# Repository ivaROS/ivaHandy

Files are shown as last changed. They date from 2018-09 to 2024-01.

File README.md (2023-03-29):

# ivaHandy

document and code for Handy arm include tutorials, mechanical files and ROS-related packages.

## Doc

Doc includes tutorials about how to build your own robot arm. Contents contain the whole process starting from
how to do assembly in Solidworks in order to make urdf generation easier to use MoveIt! setup assistant to build
your own robot arm MoveIt! package.

## mechanical

Mechanical includes 3DParts and Assembly two folders. 3DParts folder maintains all the files including Solidworks file,
3Dprinting file and drawing that belong to individual piece. Assembly holds models for the whole arm and each link.

## ros

ros folder keeps all ROS-related packages to the handy arm, which includes description, control, gazebo and MoveIt! package.
There are two versions of Handy, one is the normal model which the other one is mesh-simplified model. Each has the four above packages.

### dependencies

1. If you'd like to use finalarm_gazebo package, you should git clone balabala packages to your workspace since gazebo has dependencies on these packages if you want to load controllers in gazebo.

2. If you just need finalarm_control, finalarm_description and finalarm_moveit_config packages, in order to compile all packages out, you additionally need a package named dynamixel_motor which applies designed controllers for dynamixel motors.

### real world motion planning with Handy

Ensure that the current user is part of the `dialout` group.
If you get permission issues connecting to `/dev/ttyUSB0`, run the following and logout+login.

```bash
sudo usermod -aG dialout $USER
```

Launch handy with the following commands:

```bash
# start a node responsible for managing loaded controllers
roslaunch finalarm_control controller_manager.launch

# load configuration for individual controller
roslaunch finalarm_control start_controller.launch

# publish integrated information of controllers and transformations between links
roslaunch finalarm_description robot_state_pub.launch

# node for motion planning, collision checking, etc. jobs
roslaunch finalarm_moveit_config move_group.launch

# rviz for visualization
roslaunch finalarm_moveit_config moveit_rviz.launch

# launch the file you write for Handy to do something like picking object
roslaunch handy_experiment pick.launch
```

You can run the above using `docker-compose` instead:

```bash
docker-compose up

# node for motion planning, collision checking, etc. jobs
roslaunch finalarm_moveit_config move_group.launch

# rviz for visualization
roslaunch finalarm_moveit_config moveit_rviz.launch
```

Read [docs/docker.md](docs/docker.md) for more details.

## launchfiles

Here's a list of launch files that can be tested without access to the physical robot.

```bash
# check for urdf loading
roslaunch finalarm_description display.launch
# check robot position topics
roslaunch finalarm_description gazebo.launch
roslaunch finalarm_gazebo robot_world.launch
roslaunch finalarm_gazebo robot_world.launch control_mode:=position
# check operation of robot
roslaunch finalarm_moveit_config demo.launch
# check gazebo and moveit operate together
roslaunch finalarm_gazebo robot_world_moveit.launch

roslaunch finalarm_simplified_description display.launch
roslaunch finalarm_simplified_description gazebo.launch
roslaunch finalarm_simplified_gazebo robot_world.launch
roslaunch finalarm_simplified_gazebo robot_world_urdf.launch
roslaunch finalarm_simplified_gazebo robot_world_xacro.launch
roslaunch finalarm_simplified_moveit_config demo.launch
roslaunch finalarm_simplified_gazebo robot_world_moveit.launch
```

These are useful for manual testing, at least until some form of automated testing is implemented.

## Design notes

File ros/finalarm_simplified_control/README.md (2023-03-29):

# finalarm_simplified_control

This package redirects to most of the launch scripts in the `finalarm_control` package.
It is used to launch the controllers for the Handy arm.

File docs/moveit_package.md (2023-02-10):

# generating moveit package

Generation of moveit configuration package can be divided into two parts.
One is use moveit setup assistant to configurate your arm and the other is to modify some files within the automatically generated package.

I will just mention the key points, the rest steps you can follow the official tutorial from MoveIt!.
First you need to create group for your robot arm. Here we have two groups.
The first one is arm group and the other one is end effector group.
For the arm group, you just need setup chain for it.
Chain should starts from the root to the end effector.
For the end effector group, add links of your end effector link and two links belonged to your gripper and joints belonged to your gripper.
Secondly when configurate end effector, choose parent link to be your the end effector link and group to be your end effector group.

1. Add controllers.yaml in config folder
1. Modify finalarm_description_moveit_controller_manager.launch.xml file
1. Change the default argument of config in moveit_rviz.launch to true
1. Optional: you can turn animation loop off in `trajectory_execution.launch.xml`: `<param name="trajectory_execution/execution_duration_monitoring" value="false" />`

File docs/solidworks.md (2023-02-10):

# solidworks

## solidworks assembly

When assembling the arm in Solidworks, try to assemble the parts into different links.
For example, if your arm has 7 DOF which means it has 8 links, you need first get 8 sub-assemblies and then assemble them into the final arm assembly.

The mate between the nearby two links should be one concentric and one coincident.

## assembly to urdf

ROS has developed Solidworks add-in tool for automatical conversion from Solidworks assembly to urdf package.
Here is the link: http://wiki.ros.org/sw_urdf_exporter

There are still a lot of bugs during the process of conversion, here are some tips:

At the beginning, don't manually choose any axis, coordinate or joint type during configuration, just fill in the name of link and joint and choose the part belonged to this link. After build the whole tree of link, press export and it will automatically generate the coordinate and axis.
The joint axis should be correct if the mate is set correctly.

After automatical generation, usually the world coordinate is totally wrong, you can manually set up all coordinates.
If you don't know how to choose the coordinate, you may refer some commercial robot arms like pr2.
In order to have a end effector link, you can set up a coordinate for it and add your eef link to be child of the wrist link.
Remember the joint type between eef link and wrist link should be fixed.
The eef link just helps you conveniently do eef pose computation.
You don't need to always compensate the length of the gripper.

After coordinate is done, go back to the UI of configuration, fill in the coordinate, axis and joint type and export the configuration.
In the post-configuration menu, you can fill in the low and high limit of your joint if you choose your joint type to be revolute.
Remember the automatically generated inertial moments of link are wrong.
You should use Solidworks to get the correct inertial moments of each link relative to your coordinate.
Some mass center and mass can also be wrong.
But make sure that you can't change these parameters in the post-configuration menu.
You'd better change them directly in the urdf file.
Otherwise I assume it will affect the generation of mesh file which finally leads to the unstable of arm model in gazebo.
If you don't need to load the model in gazebo, inertial moments are irelevant to you.

When you create moveit package for your arm model and let it go somewhere, you may find some joints rotate the opposite way.
You just need to flip the joint axis in urdf file and it is fine.

## using the urdf in gazebo

The problem you may meet when load arm model in gazebo is arm is unstable and keeps shaking.
Even worst, it may explode link by link.
In order to make your arm stable in gazebo and implement control for it, here are some tips:

Firstly, turn collision and gravity off to make sure the passive behavior of your arm is correct.
Basically, the inertial moments should be the one needed modification if you generate your urdf from Solidworks.
Then add `<dynamics damping="0.5"/>` tag to each joint tag.
And the effort and velocity tag in joint limit are all zero when generated, you need to set it to a certain value.
If the arm is still unstable after the inertial moments are corrected, you can try to add tag `<implicitSpringDamper>True</implicitSpringDamper>` to each joint.
It may help.
Here is the official tutorial from gazebo, http://gazebosim.org/tutorials/?tut=ros_urdf.

2After the passive behavior of arm is correct, you are close to success and just need to implement ros control.
Here is the official tutorial from gazebo, http://gazebosim.org/tutorials/?tut=ros_control.
My suggesstion is to go through tutorial and find some examples to follow.
There may be some small problems caused by ros version.
When you meet it, just google it and you will find solution.

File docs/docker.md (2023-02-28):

# running Handy on docker and docker-compose

Handy needs python2 to run because of the serial library that is used to talk with the dynamixel motors.
This forces kinetic (possibly melodic) as the primary ROS target, which makes it difficult to use modern tooling (think opencv or pytorch) in concert with the arm.
One solution that is currently employed by the lab is to network the handy code on a machine running Ubuntu 16/18, and to run modern code on another machine.
We can also use docker to encapsulate the ROS modules in the repo, so that the host machine can be on a more modern base system.

## quickstart

Ensure the current user is part of the `dialout` (for access to `/dev/ttyUSB0`) and `docker` groups.

```bash
sudo usermod -aG dialout $USER
sudo usermod -aG docker $USER
```

Logout and login for changes to take effect.
If you are runnning an older version of Ubuntu, you may have `docker` installed, but not `docker-compose`.
Install it via pip.

```bash
pip3 install docker-compose
```

Ensure that the site-packages bin directory is on your path.

At the root of the repository, run the following commands:

```bash
# build the images for the services
docker-compose build

# run the containers
docker-compose up
```

Now you are ready to run rviz.

```bash
roslaunch finalarm_moveit_config move_group.launch
roslaunch finalarm_moveit_config moveit_rviz.launch
```

Note that the move group and the rviz commands have to be done with the same version with moveit.
If we try to run rviz commands from a noetic host on the kinetic container, we will run into protocol issues.

## Dockerfile

The `Dockerfile` contains all the dependencies for the project.
The main steps are as follows:

- Installing build dependencies (gcc, git, etc)
- Configuring `rosdep`
- Adding dynamixel dependenices
- Initializing the catkin workspace
- Adding the handy repo to the catkin workspace
- Building all dependencies

We derive our Dockerfile from `ros:kinetic-ros-core-xenial`, which lets us set an environment that can be run on any machine.
We also need to configure a catkin workspace on the container, so we can install our external dependencies and the current repo.
We end up with the following directory structure under the `/app` folder.

```
/app
├── bin
├── build
├── devel
│   ├── include
│   ├── lib
│   └── share
└── src
    ├── ivaDynamixel
    └── ivaHandy
```

We create a `bin` directory that contains useful scripts in the context of our containerized process.
The first is `ros_entrypoint.sh`, which is a simple wrapper that activates `devel/setup.bash` and runs an arbitrary command e.g. `rostopic list`.
The second script is `wait_for_topic_pattern.sh`, which we use to ensure that dependencies are created appropriately when we bring up a series of containers.

## docker-compose

The `docker-compose.yml` contains the containers necessary for running Handy.
Refer to the README for the purpose of each stage.

```mermaid
graph TD
    master
    master --> controller
    controller -.-> start_controller
    start_controller -.->|inits motors| robot_state_pub
    controller --> robot_state_pub
    robot_state_pub --> move_group

    master --> robot_state_pub
    master --> move_group
```

We create a separate master node that runs `roscore` and handles IPC between the various nodes.
Each of the processes is put into their own network i.e. the controller manager, robot state publisher, and the moveit group.
Generally in docker compose, we set up an isolated network where containers communicate with each other via internal DNS.
However, resolving hostnames of each of the containers requires us to set various parameters e.g. `ROS_HOSTNAME` and `ROS_MASTER_URI`.
Instead, we simplify the configuration by assuming that we are using the host network.
This means that all of the containers can reach each other using `localhost`, but we also lose a degree of host (and cluster) isolation.

There are a few other sections to note, if you have never used docker compose before. When using a device, we need to explicitly declare it.

```yaml
    devices:
      - /dev/ttyUSB0
    privileged: true
```

Setting `devices` here is basically the equivalent as marking it as a volume using `priviledged` mode, but is the better way to expose access to the serial device.
We also set `priviledged` to true, otherwise we run into protocol errors (presumably because of permissions, but the logging information is sparse).

We also mount our local directory into the container:

```yaml
    volumes:
      - ./:/app/src/ivaHandy/
      - ./bin:/app/bin/
```

We can change our code, and simply restart our process.
This can save us from the long build process that's caused by dependency resolution.

There is also a dependency between the different ROS nodes.
We get around this by creating a script that will look for topic creation before moving on to the next stage.
We wrap this inside of a `bash -c` call, because our entrypoint will exec a single command.
If we try to use shell commands like `&&` or `||`, we'll run into strange issues.

```yaml
    command: |
      bash -c "
        bin/wait_for_topic_pattern.sh 'finalarm_position_controller_' &&
        stdbuf -o L roslaunch --wait finalarm_description robot_state_pub.launch
      "
```

The docker-compose configuration should be treated as a reference -- the same patterns can be used on other projects too.
There are some modifications that might need to be made, such as removing the master node (if we assume that a master node exists elsewhere) or passing in an explicit `ROS_MASTER_URI`.

Additionally, here are some handy commands to keep in mind:

```bash
# shell into a new instance of a service
docker-compose run --rm ${service} bash
# e.g.
docker-compose run --rm controller_manager bash

# show the logs for a specific container
docker-compose logs -f ${service}
# e.g.
docker-compose logs -f controller_manager
```

## resources

Here are some useful links:

- https://docs.docker.com/engine/install/linux-postinstall/
- https://docs.docker.com/compose/
- http://wiki.ros.org/docker/Tutorials/Compose
- https://hub.docker.com/_/ros

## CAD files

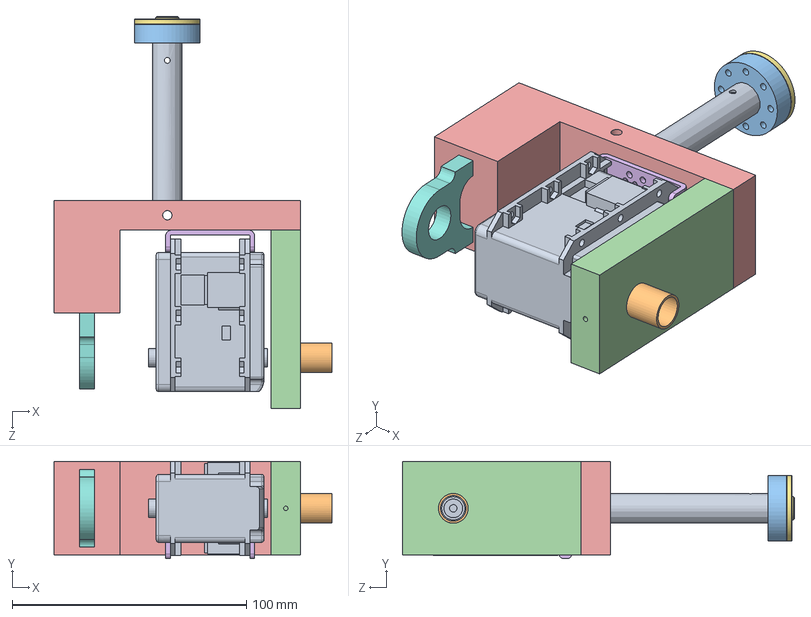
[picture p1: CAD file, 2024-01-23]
mechanical/Assembly/Link2.SLDASM
118.7 x 41.6 x 167.4 mm
at-06_Motor1
at-06-Motor2-2_v2
HN05-N101_to_at-06_attachment_6_27
Motor2Back
Motor2Bottom
FR05-S101
HN05-N101
PillowBlock
EX-106+

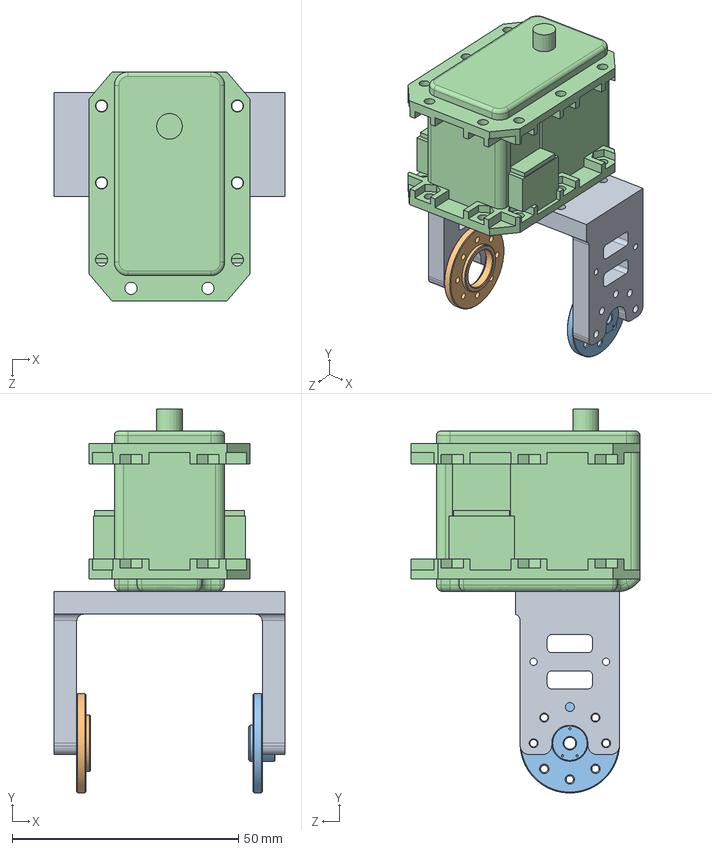
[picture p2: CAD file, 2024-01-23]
mechanical/Assembly/Link7.SLDASM
51.0 x 84.8 x 50.6 mm
myFR07-H101
HN07-i101
HN07-N101
MX-28T_R

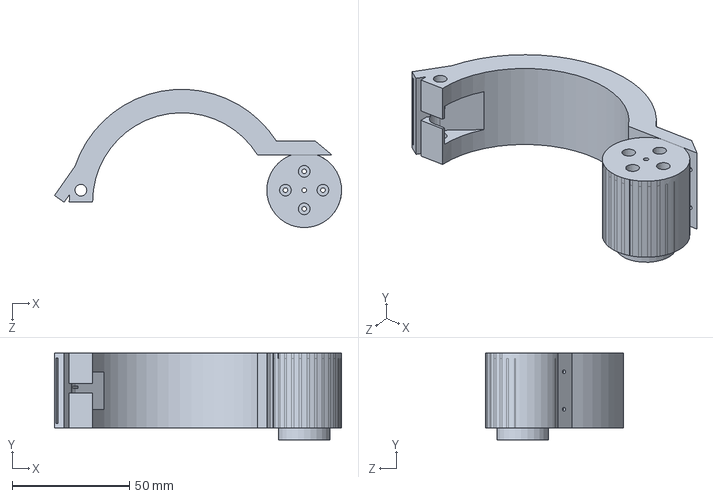
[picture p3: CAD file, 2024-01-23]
mechanical/Assembly/Link9.SLDASM
122.4 x 37.0 x 58.9 mm

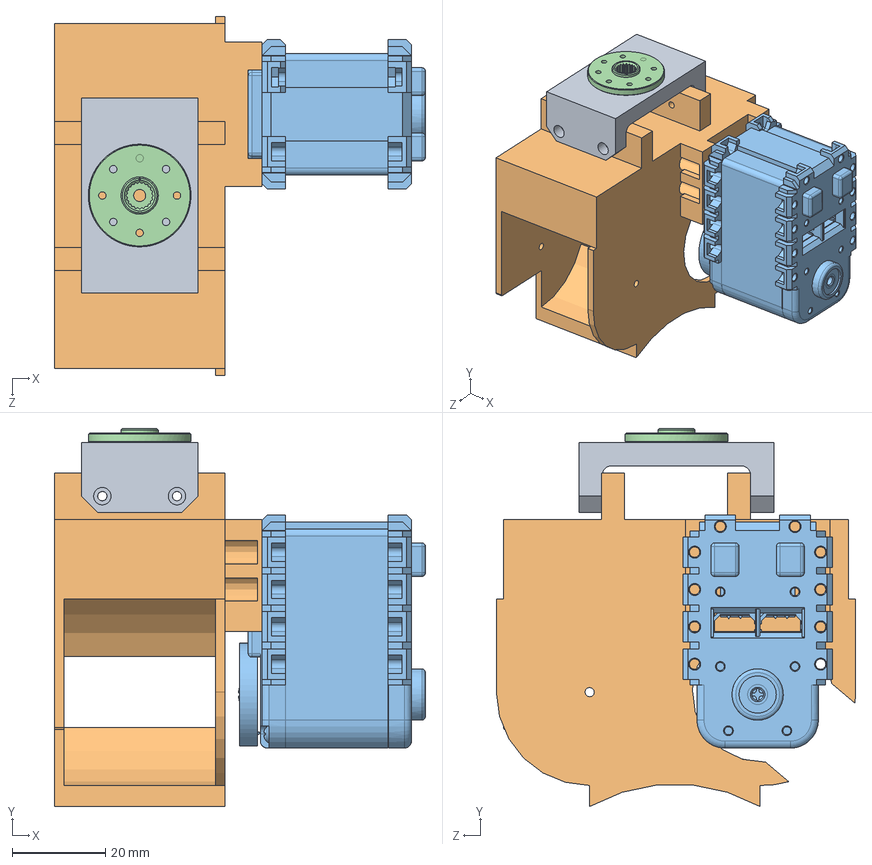
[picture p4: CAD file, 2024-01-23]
mechanical/Assembly/Link8.SLDASM
79.5 x 81.0 x 77.0 mm
GripperAttachment
supporter_cut_36_5
AX-12A
HN07-N101

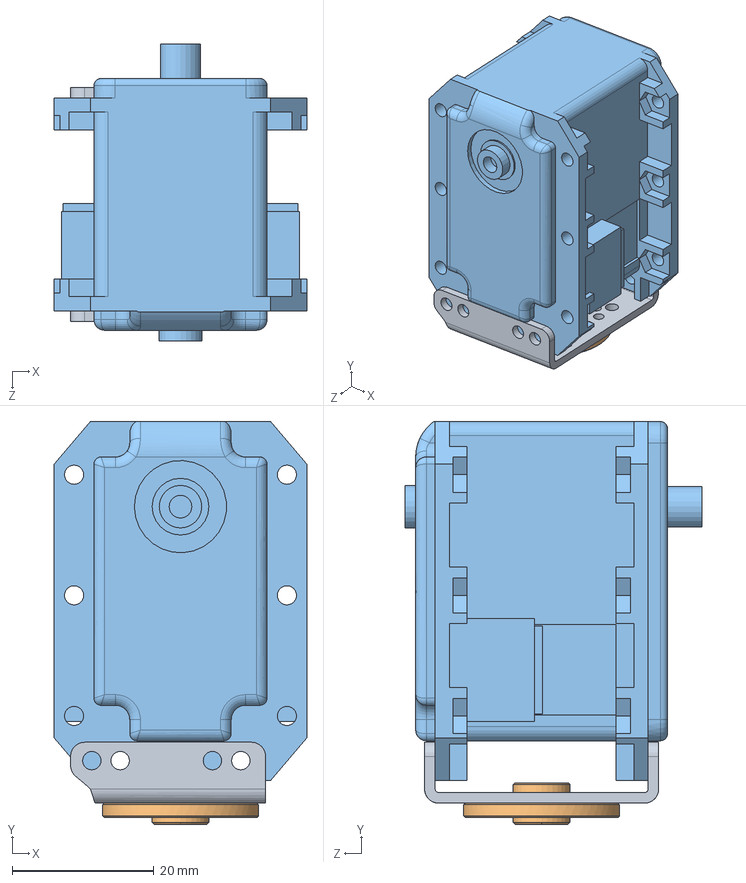
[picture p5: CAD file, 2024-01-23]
mechanical/Assembly/Link6.SLDASM
35.6 x 56.8 x 41.9 mm
FR07-S101
HN07-N101
MX-28T_R

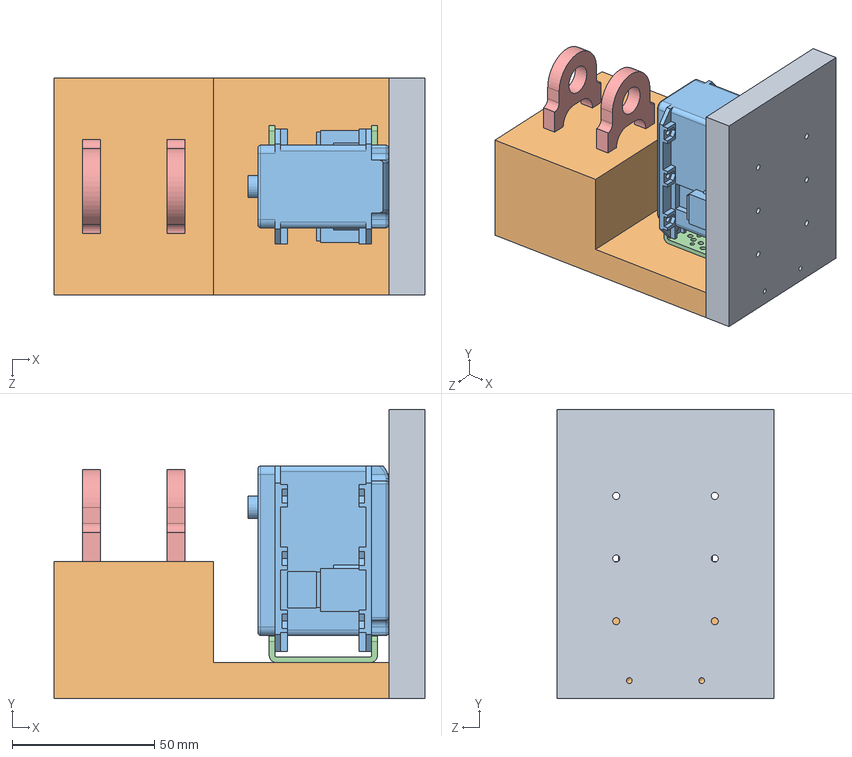
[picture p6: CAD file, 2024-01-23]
mechanical/Assembly/Link1.SLDASM
130.2 x 101.6 x 76.2 mm
Motor1Back
Motor1Bottom
EX-106+
FR05-S101
PillowBlock x 2

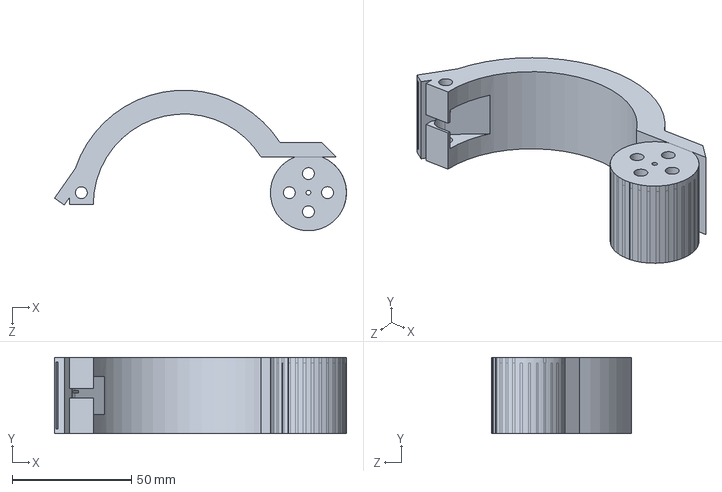
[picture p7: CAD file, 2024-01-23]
mechanical/Assembly/Link10.SLDASM
122.5 x 32.0 x 58.9 mm

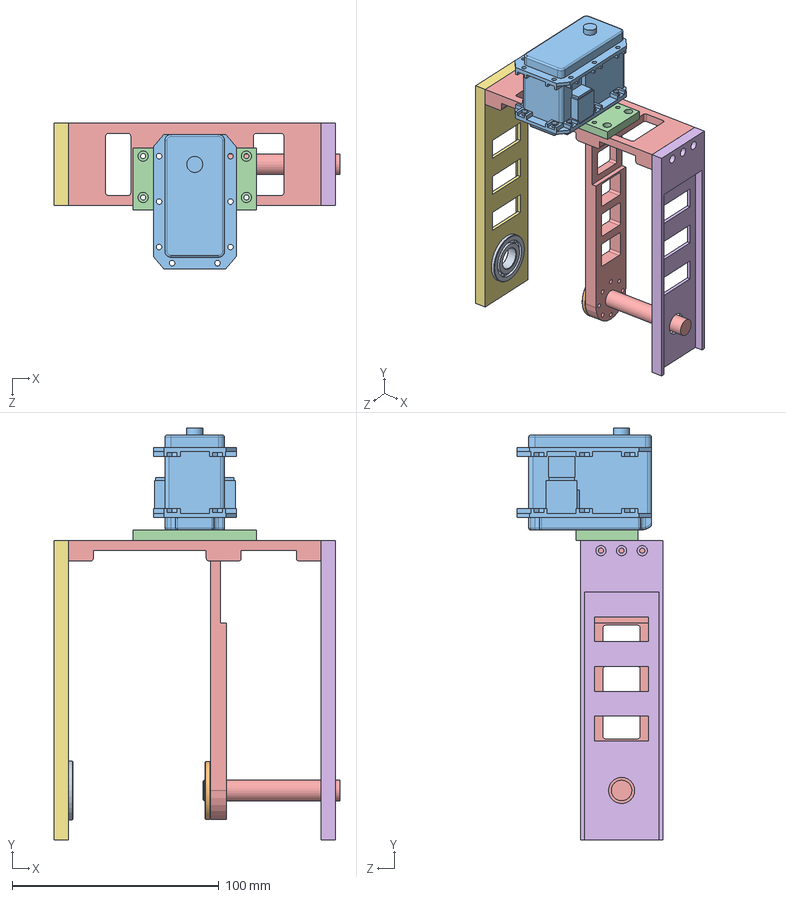
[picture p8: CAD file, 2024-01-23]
mechanical/Assembly/Link3.SLDASM
138.4 x 199.5 x 70.6 mm
BallBearing25
HN05-N101
EX-106+
adapter_ex106
Motor2Frame_HN05-N101_bug_fixed
Motor2Frame_Side1
Motor2Frame_Side2

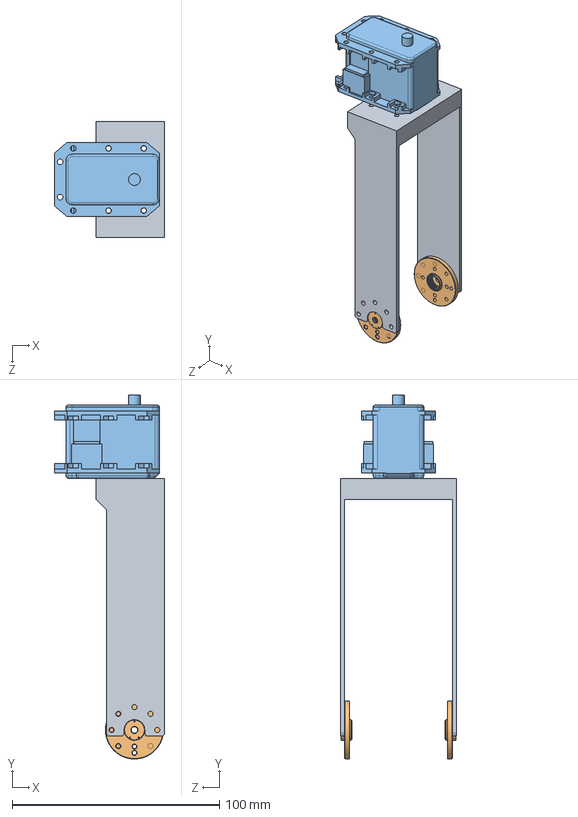
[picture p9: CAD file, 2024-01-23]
mechanical/Assembly/Link5.SLDASM
53.2 x 175.4 x 56.0 mm
myFR08-H101
HN05-N101 x 2
MX-28T_R

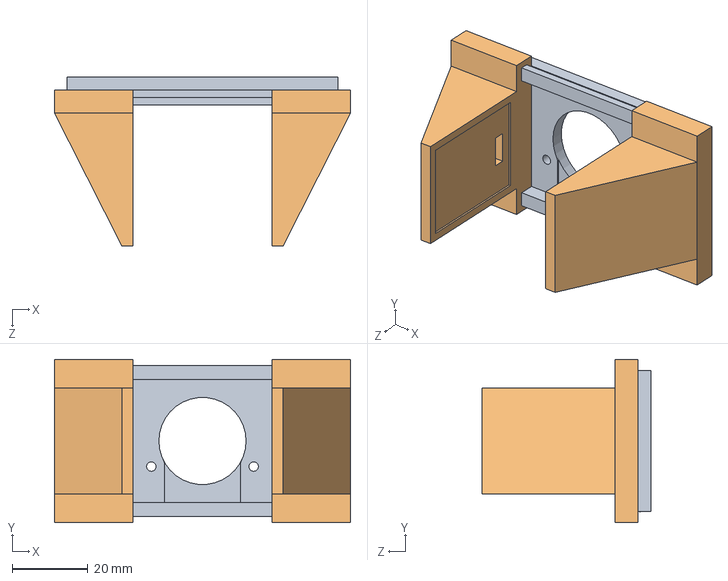
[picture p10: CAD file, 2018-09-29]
mechanical/3DParts/PrefabParts/PX-Gripper.SLDASM
78.1 x 43.0 x 44.5 mm
Guide_Rail_Fixed
Gripper_Hand_Fixed x 2

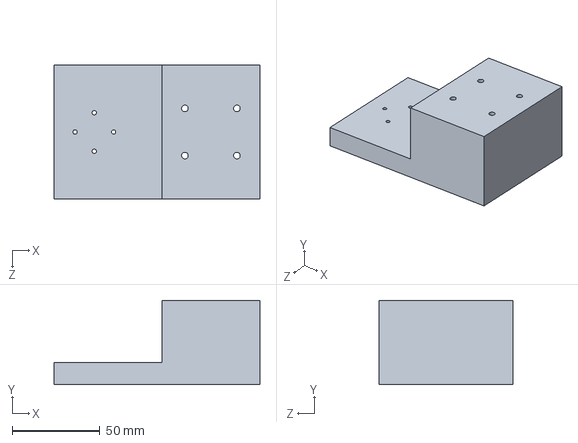
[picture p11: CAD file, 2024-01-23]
mechanical/3DParts/CustomConnectors/Link1/Motor1Bottom.SLDPRT
117.6 x 48.1 x 76.2 mm

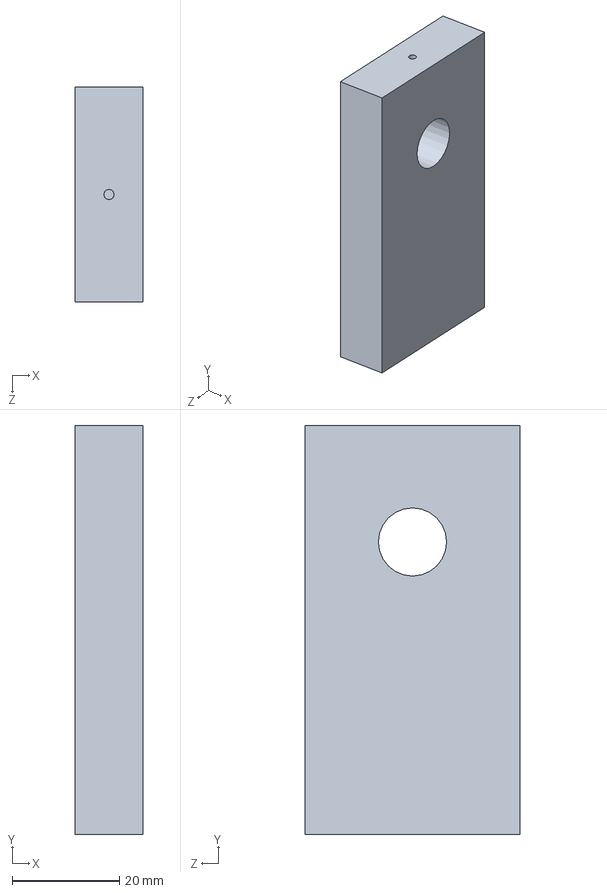
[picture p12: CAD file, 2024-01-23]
mechanical/3DParts/CustomConnectors/Link2/Motor2Back.SLDPRT
12.7 x 76.2 x 40.0 mm

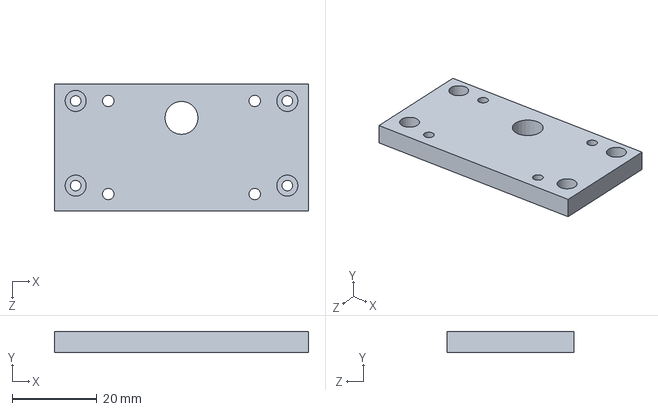
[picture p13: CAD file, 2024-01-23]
mechanical/3DParts/CustomConnectors/Link3/adapter_ex106.SLDPRT
60.0 x 5.00 x 30.0 mm

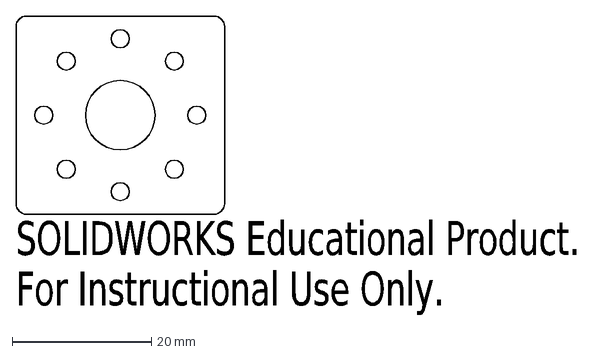
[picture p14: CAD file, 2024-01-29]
mechanical/3DParts/CustomConnectors/Link4/fabrication/HN07-N101-short-ex-ex_horn_reinforcement.DXF
SOLIDWORKS Educational Product.
For Instructional Use Only.

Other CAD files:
mechanical/Assembly/Link4.SLDASM
mechanical/Assembly/finalarm.SLDASM
mechanical/3DParts/CustomConnectors/Link10/r_Finger.SLDPRT
mechanical/3DParts/CustomConnectors/Link4/HN07-N101-short-ex-ex_side_reinforcement.SLDPRT
mechanical/3DParts/CustomConnectors/Link1/Motor1Back.SLDPRT
mechanical/3DParts/CustomConnectors/Link2/HN05-N101_to_at-06_attachment_6_27.SLDPRT
mechanical/3DParts/CustomConnectors/Link2/Motor2Bottom.SLDPRT
mechanical/3DParts/CustomConnectors/Link2/at-06-Motor2-2_v2.SLDPRT
mechanical/3DParts/CustomConnectors/Link2/at-06_Motor1.SLDPRT
mechanical/3DParts/CustomConnectors/Link3/Motor2Frame_HN05-N101_bug_fixed.SLDPRT
mechanical/3DParts/CustomConnectors/Link3/Motor2Frame_Side1.SLDPRT
mechanical/3DParts/CustomConnectors/Link3/Motor2Frame_Side2.SLDPRT
mechanical/3DParts/CustomConnectors/Link3/adapter_mx28.SLDPRT
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

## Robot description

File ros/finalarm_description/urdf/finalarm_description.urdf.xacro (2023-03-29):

<?xml version="1.0" ?>
<robot xmlns:xacro="http://www.ros.org/wiki/xacro" name="finalarm_description">
  <xacro:arg name="use_gazebo" default="false" />

  <xacro:if value="$(arg use_gazebo)">
    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

    <link name="root">
      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
    </link>

    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
    <link name="world" />
    <joint name="connect_root_and_world" type="fixed">
      <parent link="world" />
      <child link="root" />
      <axis xyz="0 0 0" />
      <origin xyz="0 0 0" rpy="0 0 0" />
    </joint>

    <joint name="root_to_base_link" type="fixed">
      <parent link="root" />
      <child link="base_link" />
      <axis xyz="0 0 0" />
      <origin xyz="0 0 0" rpy="0 0 0" />
    </joint>
  </xacro:if>

  <link name="base_link">
    <inertial>
      <origin xyz="-0.0350973236171887 2.50206915783369E-06 0.065743599294131" rpy="0 0 0" />
      <mass value="1.10920648420033" />
      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
    </inertial>
    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
  </link>
  <link name="link_2">
    <inertial>
      <origin xyz="-6.93463695862484E-06 0.00621364138420952 -0.106231333331331" rpy="0 0 0" />
      <mass value="0.471538287399183" />
      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
    </inertial>
    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
  </link>
  <joint name="joint_1" type="revolute">
    <origin xyz="0 0 0.0622" rpy="3.1416 0 3.1416" />
    <parent link="base_link" />
    <child link="link_2" />
    <axis xyz="0 0 -1" />
    <limit lower="-3.14" upper="3.14" effort="6" velocity="2.0" />
    <dynamics damping="0.5" />
  </joint>
  <link name="link_3">
    <inertial>
      <origin xyz="0.00793341258344955 -0.110904264599027 -0.00575400019431305" rpy="0 0 0" />
      <mass value="0.176545926561924" />
      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
    </inertial>
    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
  </link>
  <joint name="joint_2" type="revolute">
    <origin xyz="0 -0.00824 -0.14225" rpy="1.5708 0 0" />
    <parent link="link_2" />
    <child link="link_3" />
    <axis xyz="0 0 1" />
    <limit lower="-2.189" upper="0.0" effort="6" velocity="2.0" />
    <dynamics damping="0.5" />
  </joint>
  <link name="link_4">
    <inertial>
      <origin xyz="-1.73545194991076E-06 3.75572226324616E-05 -0.0816772034389157" rpy="0 0 0" />
      <mass value="0.104087748544112" />
      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
    </inertial>
    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
  </link>
  <joint name="joint_3" type="revolute">
    <origin xyz="0 -0.1721 -0.00754" rpy="-1.5708 0 0" />
    <parent link="link_3" />
    <child link="link_4" />
    <axis xyz="0 0 -1" />
    <limit lower="-3.14" upper="3.14" effort="6" velocity="2.0" />
    <dynamics damping="0.5" />
  </joint>
  <link name="link_5">
    <inertial>
      <origin xyz="-0.00688423968276193 0.114612027416276 -0.000499999595380635" rpy="0 0 0" />
      <mass value="0.0763995324256172" />
      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
    </inertial>
    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
  </link>
  <joint name="joint_4" type="revolute">
    <origin xyz="0 0 -0.11" rpy="-1.5708 0 0" />
    <parent link="link_4" />
    <child link="link_5" />
    <axis xyz="0 0 -1" />
    <limit lower="-2.189" upper="2.188" effort="6" velocity="2.0" />
    <dynamics damping="0.5" />
  </joint>
  <link name="link_6">
    <inertial>
      <origin xyz="1.38984233255535E-05 -3.02219879037557E-05 -0.0318489971663578" rpy="0 0 0" />
      <mass value="0.0455105599924779" />
      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
    </inertial>
    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
  </link>
  <joint name="joint_5" type="revolute">
    <origin xyz="0 0.1566 -0.0005" rpy="-1.5708 0 3.1416" />
    <parent link="link_5" />
    <child link="link_6" />
    <axis xyz="0 0 -1" />
    <limit lower="-3.14" upper="3.14" effort="6" velocity="2.0" />
    <dynamics damping="0.5" />
  </joint>
  <link name="link_7">
    <inertial>
      <origin xyz="-0.00629355961550483 0.0442792267246015 0.000326216217654773" rpy="0 0 0" />
      <mass value="0.0556423949669392" />
      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
    </inertial>
    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
  </link>
  <joint name="joint_6" type="revolute">
    <origin xyz="0 0 -0.044805" rpy="-1.5708 0 0" />
    <parent link="link_6" />
    <child link="link_7" />
    <axis xyz="0 0 1" />
    <limit lower="-2.02" upper="1.92" effort="6" velocity="2.0" />
    <dynamics damping="0.5" />
  </joint>
  <link name="link_8">
    <inertial>
      <origin xyz="-0.000582 0.01567 -0.03648" rpy="0 0 0" />
      <mass value="0.11892" />
      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
    </inertial>
    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
  </link>
  <joint name="joint_7" type="revolute">
    <origin xyz="0.0035 0.068995 0.00025" rpy="-1.5708 0 3.1416" />
    <parent link="link_7" />
    <child link="link_8" />
    <axis xyz="0 0 -1" />
    <limit lower="-3.14" upper="3.14" effort="6" velocity="2.0" />
    <dynamics damping="0.5" />
  </joint>
  <link name="link_9">
    <inertial>
      <origin xyz="0.0330748692850015 -0.0156609082500656 -0.000838888003525384" rpy="0 0 0" />
      <mass value="0.0633522380056329" />
      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
    </inertial>
    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
  </link>
  <joint name="joint_8" type="revolute">
    <origin xyz="-0.0174 0 -0.057005" rpy="1.5708 1.5708 0" />
    <parent link="link_8" />
    <child link="link_9" />
    <axis xyz="0 0 1" />
    <limit lower="-3.14" upper="3.14" effort="6" velocity="2.0" />
    <dynamics damping="0.5" />
  </joint>
  <link name="link_10">
    <inertial>
      <origin xyz="0.0338709492936103 0.0160630015014153 -0.000269069197496835" rpy="0 0 0" />
      <mass value="0.0618364235211619" />
      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
    </inertial>
    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
  </link>
  <joint name="joint_9" type="revolute">
    <origin xyz="0.0186 0 -0.056505" rpy="1.5708 1.5708 0" />
    <parent link="link_8" />
    <child link="link_10" />
    <axis xyz="0 0 1" />
    <limit lower="-3.14" upper="3.14" effort="6" velocity="2.0" />
    <dynamics damping="0.5" />
  </joint>
  <link name="link_eef" />
  <joint name="joint_eef" type="fixed">
    <origin xyz="0 0 -0.15225" rpy="3.1416 0 3.1416" />
    <parent link="link_8" />
    <child link="link_eef" />
    <axis xyz="0 0 0" />
  </joint>

  <xacro:if value="$(arg use_gazebo)">
    <xacro:macro name="static_no_collide" params="reference">
      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
    </xacro:macro>

    <xacro:static_no_collide reference="base_link" />
    <xacro:static_no_collide reference="link_1" />
    <xacro:static_no_collide reference="link_2" />
    <xacro:static_no_collide reference="link_3" />
    <xacro:static_no_collide reference="link_4" />
    <xacro:static_no_collide reference="link_5" />
    <xacro:static_no_collide reference="link_6" />
    <xacro:static_no_collide reference="link_7" />
    <xacro:static_no_collide reference="link_8" />
    <xacro:static_no_collide reference="link_9" />
    <xacro:static_no_collide reference="link_10" />

    <xacro:macro name="joint_implicit_damper" params="reference">
      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
    </xacro:macro>

    <xacro:joint_implicit_damper reference="joint_1" />
    <xacro:joint_implicit_damper reference="joint_2" />
    <xacro:joint_implicit_damper reference="joint_3" />
    <xacro:joint_implicit_damper reference="joint_4" />
    <xacro:joint_implicit_damper reference="joint_5" />
    <xacro:joint_implicit_damper reference="joint_6" />
    <xacro:joint_implicit_damper reference="joint_7" />
    <xacro:joint_implicit_damper reference="joint_8" />
    <xacro:joint_implicit_damper reference="joint_9" />

    <xacro:macro name="transmission" params="name joint actuator">
      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
    </xacro:macro>

    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
    <xacro:transmission name="tran1" joint="joint_1" actuator="motor_1" />
    <xacro:transmission name="tran2" joint="joint_2" actuator="motor_2" />
    <xacro:transmission name="tran3" joint="joint_3" actuator="motor_3" />
    <xacro:transmission name="tran4" joint="joint_4" actuator="motor_4" />
    <xacro:transmission name="tran5" joint="joint_5" actuator="motor_5" />
    <xacro:transmission name="tran6" joint="joint_6" actuator="motor_6" />
    <xacro:transmission name="tran7" joint="joint_7" actuator="motor_7" />
    <xacro:transmission name="tran8" joint="joint_8" actuator="motor_8" />
    <xacro:transmission name="tran9" joint="joint_9" actuator="motor_9" />
  </xacro:if>
</robot>

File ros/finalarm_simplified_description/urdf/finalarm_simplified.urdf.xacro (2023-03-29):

<?xml version="1.0" ?>
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
<robot name="finalarm_simplified" xmlns:xacro="http://www.ros.org/wiki/xacro">
  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
  <xacro:include filename="$(find finalarm_simplified_description)/urdf/finalarm_simplified.gazebo" />

  <link name="root">
    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
  </link>

  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
  <link name="world" />

  <joint name="connect_root_and_world" type="fixed">
    <parent link="world" />
    <child link="root" />
    <axis xyz="0 0 0" />
    <origin xyz="0 0 0" rpy="0 0 0" />
  </joint>

  <joint name="root_to_base_link" type="fixed">
    <parent link="root" />
    <child link="base_link" />
    <axis xyz="0 0 0" />
    <origin xyz="0 0 0" rpy="0 0 0" />
  </joint>

  <link name="base_link">
    <inertial>
      <origin xyz="-0.0164 -8.67361737988404E-19 0.0311" rpy="0 0 0" />
      <mass value="0.481547424" />
      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
    </inertial>
    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
  </link>
  <link name="link_2">
    <inertial>
      <origin xyz="-1.38777878078145E-17 -4.33680868994202E-18 -0.078375" rpy="0 0 0" />
      <mass value="0.7142784" />
      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
    </inertial>
    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
  </link>
  <joint name="joint_1" type="revolute">
    <origin xyz="0 0 0.0622" rpy="3.1416 0 3.1416" />
    <parent link="base_link" />
    <child link="link_2" />
    <axis xyz="0 0 -1" />
    <limit lower="-3.14" upper="3.14" effort="6" velocity="2" />
    <dynamics damping="0.5" />
  </joint>
  <link name="link_3">
    <inertial>
      <origin xyz="0.00913796893535261 -0.110721113647521 0.000700000000000008" rpy="0 0 0" />
      <mass value="0.26363602" />
      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
    </inertial>
    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
  </link>
  <joint name="joint_2" type="revolute">
    <origin xyz="0 0 -0.14225" rpy="1.5708 0 0" />
    <parent link="link_2" />
    <child link="link_3" />
    <axis xyz="0 0 1" />
    <limit lower="-2.35" upper="2.35" effort="6" velocity="2" />
    <dynamics damping="0.5" />
  </joint>
  <link name="link_4">
    <inertial>
      <origin xyz="0 -8.67361737988404E-19 -0.06225" rpy="0 0 0" />
      <mass value="0.2302254" />
      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
    </inertial>
    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
  </link>
  <joint name="joint_3" type="revolute">
    <origin xyz="0 -0.1721 0.0007" rpy="-1.5708 0 0" />
    <parent link="link_3" />
    <child link="link_4" />
    <axis xyz="0 0 -1" />
    <limit lower="-3.14" upper="3.14" effort="6" velocity="2" />
    <dynamics damping="0.5" />
  </joint>
  <link name="link_5">
    <inertial>
      <origin xyz="-0.00941019053261395 0.12018845656372 -0.00050000000000005" rpy="0 0 0" />
      <mass value="0.09729148" />
      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
    </inertial>
    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
  </link>
  <joint name="joint_4" type="revolute">
    <origin xyz="0 0 -0.11" rpy="-1.5708 0 0" />
    <parent link="link_4" />
    <child link="link_5" />
    <axis xyz="0 0 -1" />
    <limit lower="-2.6" upper="2.6" effort="6" velocity="2" />
    <dynamics damping="0.5" />
  </joint>
  <link name="link_6">
    <inertial>
      <origin xyz="0 0 -0.0284" rpy="0 0 0" />
      <mass value="0.0717838399999999" />
      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
    </inertial>
    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
  </link>
  <joint name="joint_5" type="revolute">
    <origin xyz="0 0.1551 -0.0005" rpy="-1.5708 0 3.1416" />
    <parent link="link_5" />
    <child link="link_6" />
    <axis xyz="0 0 -1" />
    <limit lower="-3.14" upper="3.14" effort="6" velocity="2" />
    <dynamics damping="0.5" />
  </joint>
  <link name="link_7">
    <inertial>
      <origin xyz="-0.00826463614894074 0.044192432559462 0.000250000000000077" rpy="0 0 0" />
      <mass value="0.07582828" />
      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
    </inertial>
    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
  </link>
  <joint name="joint_6" type="revolute">
    <origin xyz="0 0 -0.0448" rpy="-1.5708 0 0" />
    <parent link="link_6" />
    <child link="link_7" />
    <axis xyz="0 0 1" />
    <limit lower="-1.75" upper="1.75" effort="6" velocity="2" />
    <dynamics damping="0.5" />
  </joint>
  <link name="link_8">
    <inertial>
      <origin xyz="-0.00258077730485411 0.00608919416388292 -0.0569223421804808" rpy="0 0 0" />
      <mass value="0.4263865924" />
      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
    </inertial>
    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
  </link>
  <joint name="joint_7" type="revolute">
    <origin xyz="0.0035 0.0665 0.00025" rpy="-1.5708 0 3.1416" />
    <parent link="link_7" />
    <child link="link_8" />
    <axis xyz="0 0 -1" />
    <limit lower="-3.14" upper="3.14" effort="6" velocity="2" />
    <dynamics damping="0.5" />
  </joint>
  <link name="link_eef" />
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

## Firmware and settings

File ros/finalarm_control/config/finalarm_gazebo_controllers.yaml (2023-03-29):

finalarm_position_controller_1: &joint
  type: position_controllers/JointPositionController
  joint: joint_1
  pid: {p: 10000, i: 0.01, d: 0.0}

finalarm_position_controller_2:
  <<: *joint
  joint: joint_2

finalarm_position_controller_3:
  <<: *joint
  joint: joint_3

finalarm_position_controller_4:
  <<: *joint
  joint: joint_4

finalarm_position_controller_5:
  <<: *joint
  joint: joint_5

finalarm_position_controller_6:
  <<: *joint
  joint: joint_6

finalarm_position_controller_7:
  <<: *joint
  joint: joint_7

finalarm_position_controller_8:
  type: position_controllers/JointPositionController
  joint: joint_8
  pid: {p: 1000, i: 0.01, d: 0.0}

finalarm_position_controller_9:
  type: position_controllers/JointPositionController
  joint: joint_9
  pid: {p: 1000, i: 0.01, d: 0.0}

finalarm_joint_state_controller:
  type: joint_state_controller/JointStateController
  publish_rate: 50

# Note: the position controllers and trajectory controllers are exclusive to
# each other. If you spawn both, you will get an error.
finalarm_joint_trajectory_action_controller:
  type: position_controllers/JointTrajectoryController
  joints:
    - joint_1
    - joint_2
    - joint_3
    - joint_4
    - joint_5
    - joint_6
    - joint_7

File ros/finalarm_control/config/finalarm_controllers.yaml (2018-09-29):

finalarm_position_controller_1:
    controller:
        package: dynamixel_controllers
        module: joint_position_controller
        type: JointPositionController
    joint_name: joint_1
    joint_speed: 1.5
    joint_compliance_margin: 1
    joint_compliance_slope: 4
    motor:
        id: 1
        init: 2048
        min: 0
        max: 4096
        bias: 0.39269908169 #-0.528617013529 #-0.608617013529

finalarm_position_controller_2:
    controller:
        package: dynamixel_controllers
        module: joint_position_controller
        type: JointPositionController
    joint_name: joint_2
    joint_speed: 1.5
    joint_compliance_margin: 1
    joint_compliance_slope: 4
    motor:
        id: 2
        init: 2048
        min: 0
        max: 4096
        bias: 0 #-0.160377691373

finalarm_position_controller_3:
    controller:
        package: dynamixel_controllers
        module: joint_position_controller
        type: JointPositionController
    joint_name: joint_3
    joint_speed: 1.5
    motor:
        id: 3
        init: 2048
        min: 0
        max: 4096

finalarm_position_controller_4:
    controller:
        package: dynamixel_controllers
        module: joint_position_controller
        type: JointPositionController
    joint_name: joint_4
    joint_speed: 1.5
    joint_compliance_margin: 1
    joint_compliance_slope: 4
    motor:
        id: 4
        init: 2048
        min: 0
        max: 4096

finalarm_position_controller_5:
    controller:
        package: dynamixel_controllers
        module: joint_position_controller
        type: JointPositionController
    joint_name: joint_5
    joint_speed: 1.5
    motor:
        id: 5
        init: 2048
        min: 0
        max: 4096

finalarm_position_controller_6:
    controller:
        package: dynamixel_controllers
        module: joint_position_controller
        type: JointPositionController
    joint_name: joint_6
    joint_speed: 1.5
    motor:
        id: 6
        init: 2048
        min: 0
        max: 4096
        bias: 0

finalarm_position_controller_7:
    controller:
        package: dynamixel_controllers
        module: joint_position_controller
        type: JointPositionController
    joint_name: joint_7
    joint_speed: 1.5
    motor:
        id: 7
        init: 2048
        min: 0
        max: 4096

finalarm_position_controller_8:
    controller:
        package: dynamixel_controllers
        module: joint_position_controller
        type: JointPositionController
    joint_name: joint_8
    joint_speed: 1.5
    joint_torque_limit: 1.0
    motor:
        id: 8
        init: 512
        min: 0 #400
        max: 1023 #611

finalarm_position_controller_9:
    controller:
        package: dynamixel_controllers
        module: joint_position_controller
        type: JointPositionController
    joint_name: joint_9
    joint_speed: 1.5
    joint_torque_limit: 1.0
    motor:
        id: 9
        init: 512
        min: 0 #400
        max: 1023 #611

finalarm_joint_trajectory_action_controller:
    controller:
        package: dynamixel_controllers
        module: joint_trajectory_action_controller
        type: JointTrajectoryActionController
    joint_trajectory_action_node:
        min_velocity: 0.5
        constraints:
            goal_time: 5.0

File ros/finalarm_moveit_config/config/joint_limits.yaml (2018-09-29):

# joint_limits.yaml allows the dynamics properties specified in the URDF to be overwritten or augmented as needed
# Specific joint properties can be changed with the keys [max_position, min_position, max_velocity, max_acceleration]
# Joint limits can be turned off with [has_velocity_limits, has_acceleration_limits]
joint_limits:
  joint_1:
    has_velocity_limits: false
    max_velocity: 0
    has_acceleration_limits: false
    max_acceleration: 0
  joint_2:
    has_velocity_limits: false
    max_velocity: 0
    has_acceleration_limits: false
    max_acceleration: 0
  joint_3:
    has_velocity_limits: false
    max_velocity: 0
    has_acceleration_limits: false
    max_acceleration: 0
  joint_4:
    has_velocity_limits: false
    max_velocity: 0
    has_acceleration_limits: false
    max_acceleration: 0
  joint_5:
    has_velocity_limits: false
    max_velocity: 0
    has_acceleration_limits: false
    max_acceleration: 0
  joint_6:
    has_velocity_limits: false
    max_velocity: 0
    has_acceleration_limits: false
    max_acceleration: 0
  joint_7:
    has_velocity_limits: false
    max_velocity: 0
    has_acceleration_limits: false
    max_acceleration: 0
  joint_8:
    has_velocity_limits: false
    max_velocity: 0
    has_acceleration_limits: false
    max_acceleration: 0
  joint_9:
    has_velocity_limits: false
    max_velocity: 0
    has_acceleration_limits: false
    max_acceleration: 0

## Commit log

2018-09-29 handy codes include document, mechanical and ros-related codes
    [AX-12A.SLDPRT, BallBearing25.SLDPRT, EX-106+.SLDPRT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]
2023-02-10 Add docker-compose configuration for running Handy (#3)
    * Consolidate docs into markdown files
    * Add initial dockerfile configuration
    * Update dockerfile and compose with more controller methods
    * Fix whitespacing issues (tabs/spaces)
    * Refactor torque and state publisher scripts
    * Use functools partial instead of lambda
    * Use --include-eol-distros in rosdep
    * Add successful docker-compose configuration for handy rviz
    * Add docs for docker
    [disable_torque_handy.py, finalarm_joint_state_publisher.py]
2023-03-29 Update control, description, and gazebo packages for rviz/moveit control (#6)
    * wip: modify gazebo controllers for updated descriptions
    * Add successful gazebo run with trajectory controller
    * Update position control for gazebo
    * Remove unncessary torque controller and rename launch files for clarity
    * Remove most scripts
    We only need a single script to handle disabling torque on the motors
    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
    [controllers.yaml, finalarm_controllers.yaml, finalarm_description.urdf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]
2024-01-23 update to SW version 2023
    [AX-12A.SLDPRT, BallBearing25.SLDPRT, EX-106+.SLDPRT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]
2024-01-23 refine link4 design; add aluminum reinforcement plates (sides & horn)
    [HN07-N101-short-ex-ex_horn_reinforcement.SLDPRT, HN07-N101-short-ex-ex_side_reinforcement.SLDPRT, HN07-N101-short-ex-ex_v2.SLDPRT]
2024-01-23 finalized link4 revision
    [HN07-N101-short-ex-ex_horn_reinforcement.SLDPRT, HN07-N101-short-ex-ex_side_reinforcement.SLDPRT, HN07-N101-short-ex-ex_v2.SLDPRT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]
2024-01-23 fabrication specs/artifacts
    [HN07-N101-short-ex-ex_side_reinforcement.SLDPRT, HN07-N101-short-ex-ex_v2.STL, reinforcement_cutout_patterns.DXF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]
2024-01-29 re-generate fab files for laser cut
    [HN07-N101-short-ex-ex_horn_reinforcement.DXF, HN07-N101-short-ex-ex_side_reinforcement.DXF, reinforcement_cutout_patterns.DXF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]
